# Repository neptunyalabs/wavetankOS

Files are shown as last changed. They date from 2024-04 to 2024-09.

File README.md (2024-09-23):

# What Is This:
Wavetank OS is a do-it-yourself wave tank solution. For those in need of an in-office or in-classroom wavetank with a cloud based (AWS S3) data acquisition program this might be the cheapest & easiest way to get started. 

> [!CAUTION]
> This project comes with no guarantee of performance, or safety. In fact with the combination of electricity and a few hundred gallons of water, as well as fast moving mechanical parts We suggest only experienced makers attempt this project as there are many ways to hurt or kill yourself.

#### The Wavetank
The completed wave tank shown below
Wave Tank Example

#### Example Data
Example data quality post-processed with the `wavepost` utility
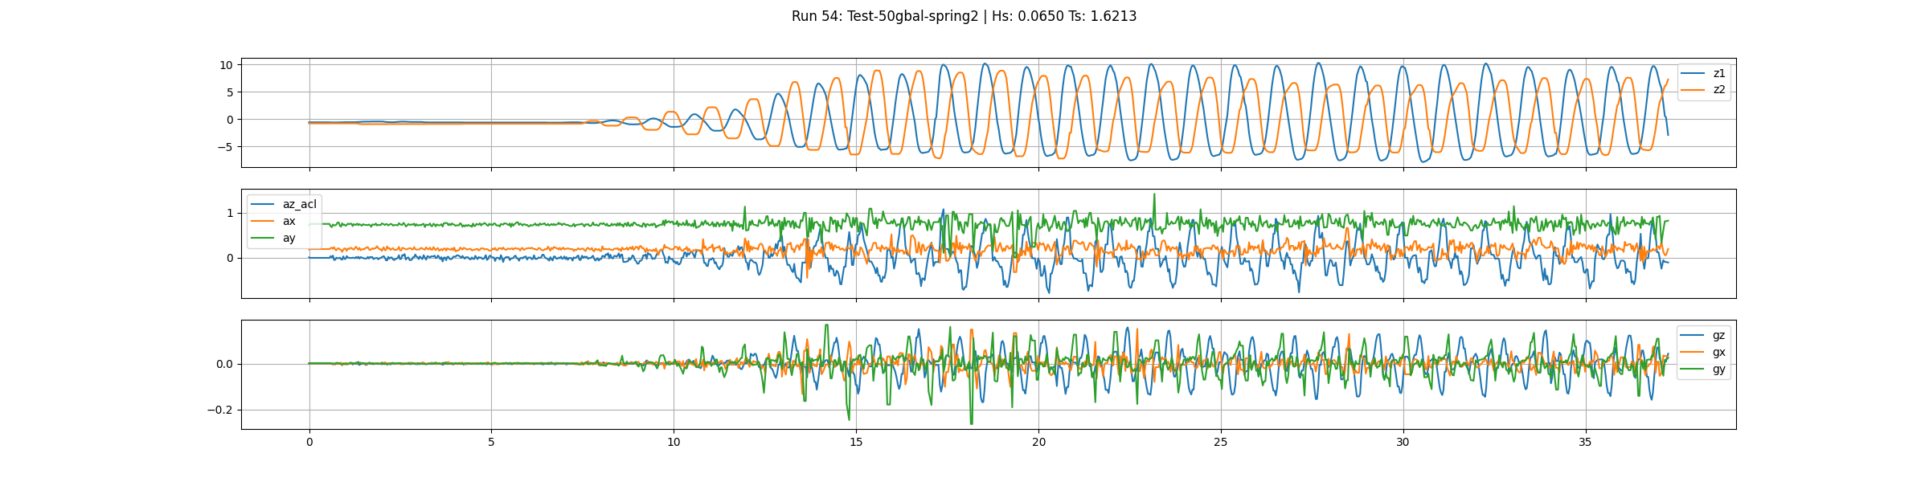
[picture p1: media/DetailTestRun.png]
Example Run


# What Is Included:
1. a set of structural plans, a bom, and construction guidance for the physical wavetank.
2. a bill of materials for electronic components as well as pcb schematics and design files. The design only requires soldering connections and headers so this is beginner friendly
3. this python package that runs a S3 data acquisition, wave maker control, and a live dashboard service to control and view the data in real time, based on pigpio.
4. electronics & software setup guide
5. a post-processing data cli `wavepost` that pulls data from S3 storage and creates graphs of each test run

#  What kind of measurements are provided:
- 4 Encoder positions with RS-485 differential output, we recommend using a magnetic linear scale for its no friction, waterproof design.
- 4 Ultrasonic Distance channels available for capturing wave height.
- Several Channels Of ADC with a dedicated IC chip.
- An integration with an MPU9250 9 axis (Accel,Gyro,Magnetometer) capture
- A few extra outputs for I2C and debugging
- Proven data-rate is between 100 samples per second to S3 storage.

# How To:
Below you'll find a mostly complete set of items you'll need to have to construct the wavetank system.

### Construction Instructions:
1. Tank Construction & Assembly [here](CONSTRUCTION.md)
2. Electronics Construction Overview [here](ELECTRONICS.md)

### Bill of Materials (BOM)
The bill of materials is located here, if you have questions on something feel free to leave a comment, or if you want to contribute an alternative idea feel free suggest alternatives.
https://docs.google.com/spreadsheets/d/107yxzDKXDjfQvaocU3NCo5I_NLpH0Xee_oWynt8TL3E/edit?usp=sharing

### PCB Design Files:
You can order your PCB's from this website, as well as modify the design. If you do make significant improvements to the design please fork this project and submit a PR with your design files.
https://oshwlab.com/neptunya/waveware

### Project Share Folder:
Please see additional media for the construction of the wave tank or assembly of the electronics
https://drive.google.com/drive/folders/0AGw2YOvWZK7JUk9PVA

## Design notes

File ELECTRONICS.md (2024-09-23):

# Electronics Assembly

## Hardware Setup

### PCB Overview
the PCB acts as a connection between the raspberry pi and a number of peripheral sensors and actuators.
#TODO: connections & placement overview (photo)
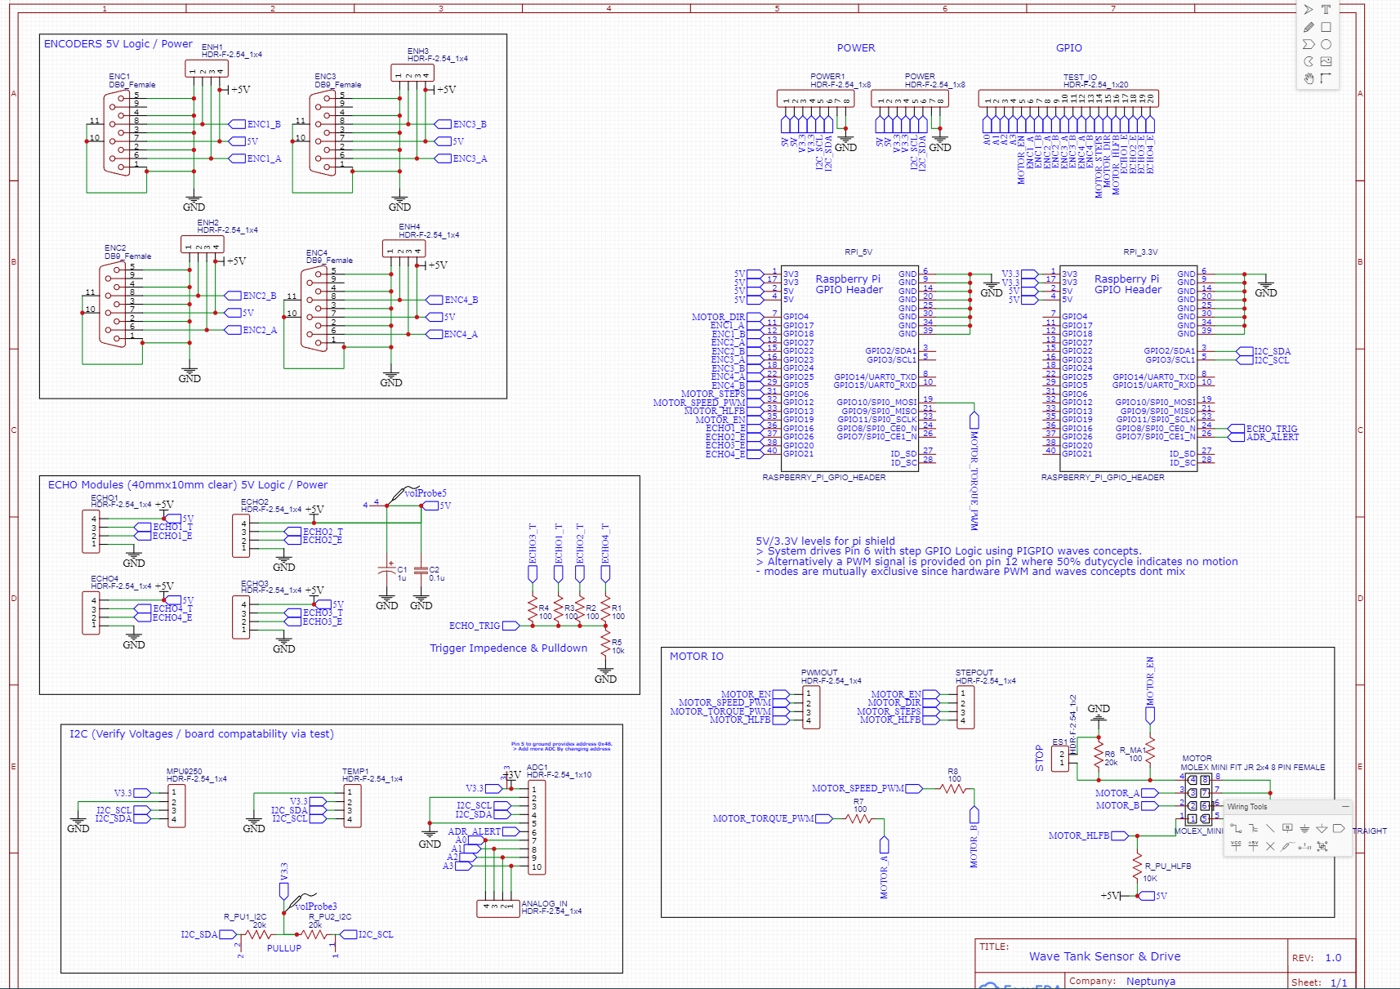
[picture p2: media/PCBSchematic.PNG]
PCB Schematic


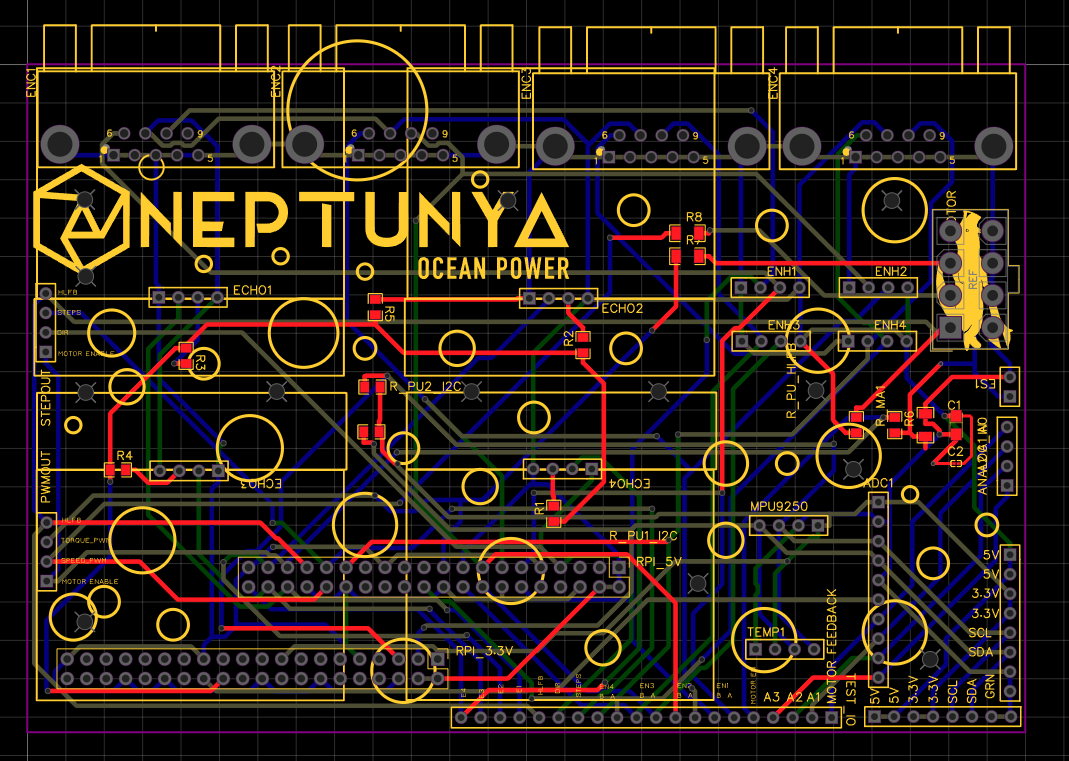
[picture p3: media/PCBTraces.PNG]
PCB Board


## Linux Setup
1. Using the BOM below find the purchase & setup links for the raspberry pi and install ubuntu 20.04 or later
2. Once installed & booted, either log on remotely using SSH or using a mouse & keyboard then navigate to the home directory using `cd ~/`
3. Download the setup script to install all utilities 
```
curl https://raw.githubusercontent.com/neptunyalabs/wavetankOS/main/setup.sh -o wavetankOS_install.sh
```

4. Install wavetankOS, this will enable the wavetank service to start on startup. 
```
bash ~/wavetankOS_install.sh
```
5. If you'd like to use AWS S3 data logging you will need to configure your aws account by adding the account apikey and secret in the environmental variable section, or use another method that AWS provides with their BOTO3 CLI utility. Try running `aws configure` to get started.

Your wavetank dashboard will now be running here `http://<your_hostname>.local:8050/`

### Setting Up The Software:
Configuration of the software is handled through environmental variables, these can be edited for the wavetank service by editing the `/lib/systemd/system/wavetank.service` file on your raspberry pi

This example `service` created in a bash "one-liner" lists the environmental variable defaults
```
sudo bash -c '/bin/cat <<EOM >"/lib/systemd/system/wavetank.service"
[Unit]
WaveTankOS Firmware & Dashboard
[Service]
ExecStart=/home/$(whoami)/wavetankOS/waveware/fw_main.py
ExecStop=/bin/systemctl kill -s SIGKILL wavetank
Type=forking

#here are the potential enviornmental varables for your use
#Environment="WAVEWARE_LOG_S3=true"
#Environment="WAVEWARE_S3_BUCKET=custom_aws_bucket_name" 
#Environment="WAVEWARE_FLDR_NAME=v1" 
#Environment="WAVEWARE_PORT=8777"  #where to run the daq / control api
#Environment="FW_HOST=0.0.0.0"  #where to run the daq / control api
#Environment="WAVEWARE_VWAVE_DIRECT=true"  #control based on speed with correction
#Environment="WAVE_SPEED_DRIVE_MODE=pwm"  #use 'step','pwm','off','step-pwm' depending on your motor type

#Dashboard Customization
#Environment="WAVEWARE_DASH_GRAPH_UPT=3.3"
#Environment="WAVEWARE_DASH_READ_UPT=1.5"

#DAQ Rates
#Environment="WAVEWARE_POLL_RATE=0.033"
#Environment="WAVEWARE_POLL_TEMP=60"
#Environment="WAVEWARE_WINDOW=6" #wavelengths to show for buffer size

[Install]
WantedBy=multi-user.target

EOM'
```

Additionally you can change any one of these when running manually using instructions below.

##### Running Manually:
1. stop the wavetank service `sudo systemctl stop wavetank`
2. use `wavedash` to run the live dashboard
3. use `wavedaq` to run the data acquisition system and control system
4. use `wavepost` to run a post-processing system that downloads data from S3, use `wavepost -h` to determine options. Set the test-data download directory to `WAVEWARE_TESTDATA_FLDR` as the root, then to the `WAVEWARE_FLDR_NAME` of your test data, by default this will be `V1` and must match the data on S3 to be successful. 

### Using The Software:
While using a computer on the same network as the raspberry pi navigate to `http://<your_hostname>.local:8050/` in your browser of choice.

#### Dashboard Overview
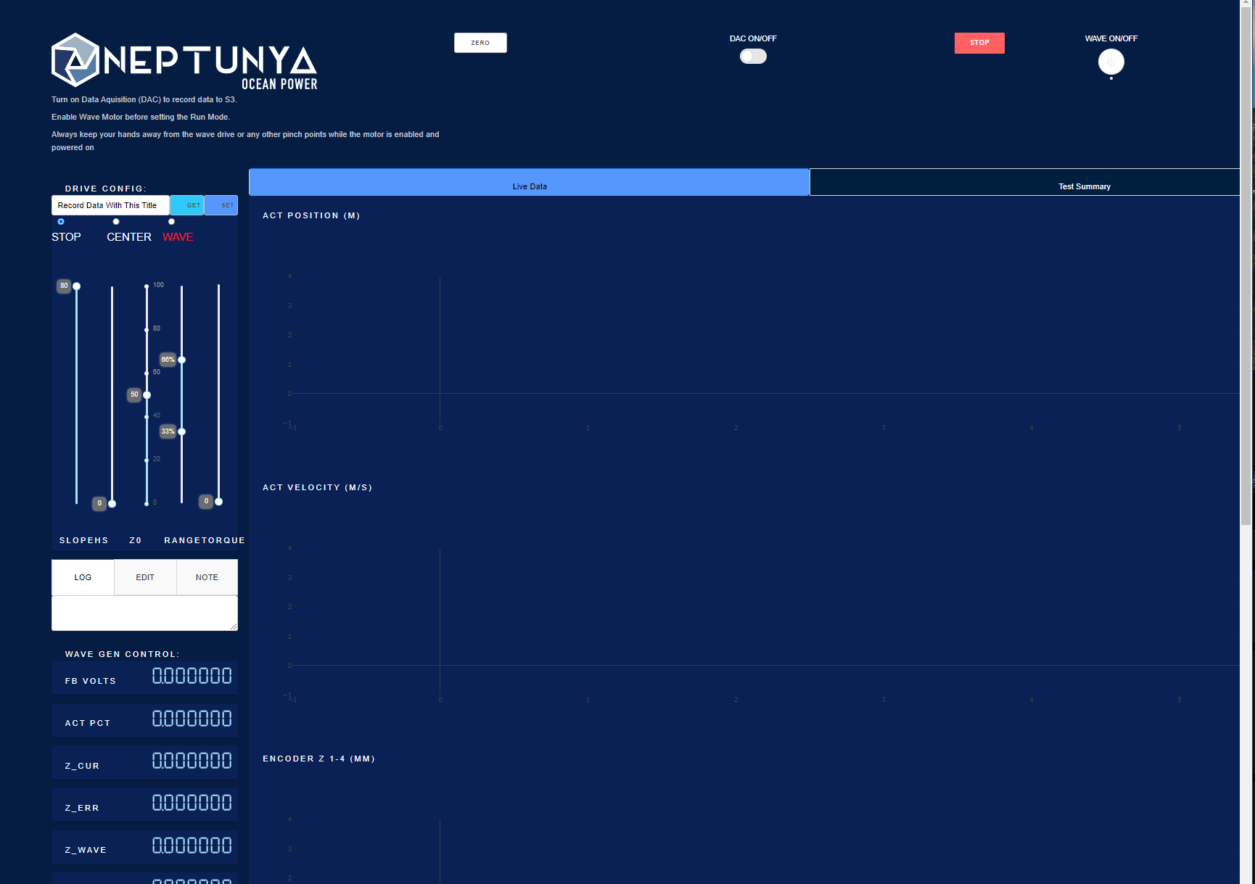
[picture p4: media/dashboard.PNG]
Dashboard Overview


##### Drive Config Section:
1. enable the motor controller with the `wave on/off` button
2. mode input sets the drive mode for the wave maker. Use the get/set buttons to apply changes or get the current state of the wavemaker drive.
3. Set the mode of operation, it is recommened to center first towards the `Zo` input that is a value of 1-100 between the `range` slider values.
4. set the wave height and slope `(wave length x0.5/ wave height)`
5. Using the clearpath PWM mode allows setting torque at right
6. At any time press the red stop button and the drive config will be set to stop. It is safter to use a power cutoff to the motor driver but this works as well.

##### Data Output:
1. encoder readouts can be zero'd by using the zero button. This is useful for ensuring zero is at some datum.
2. By turning on the DAQ with the slider data will start populating from the running daq application.
3. the readouts and positions on the graphs will update as your tests goes on and as long as the daq is on.
4. Finally the test-summary allows a review of all test-points run and their stats.

##### Logging / Customization & Test Notes:
1. The test-note function allows the recording to S3 of test-notes to help with recording intent of tests, or anomolies in the process, or record any other data that you want.
2. The edit tab allows safe setting & adjustment of control system parameters and other internal variables. This can be dangerous however restarting the process or device will fix any error.
3. Finally the log will display the feedback of the DAQ & Control system to give the user an idea of what is going on.

##### Post Processing:
you can easily download your processed data as either a csv or image by using this command. Be sure to set `WAVEWARE_FLDR_NAME` for the output of your data, or use both `WAVEWARE_TESTDATA_DIR` \ `WAVEWARE_FLDR_NAME` as your root folder. This defaults to the fifth folder above the postprocessing file, you've been warned!
```bash
wavepost --run-all --run-all
```

An example set of data is shown below
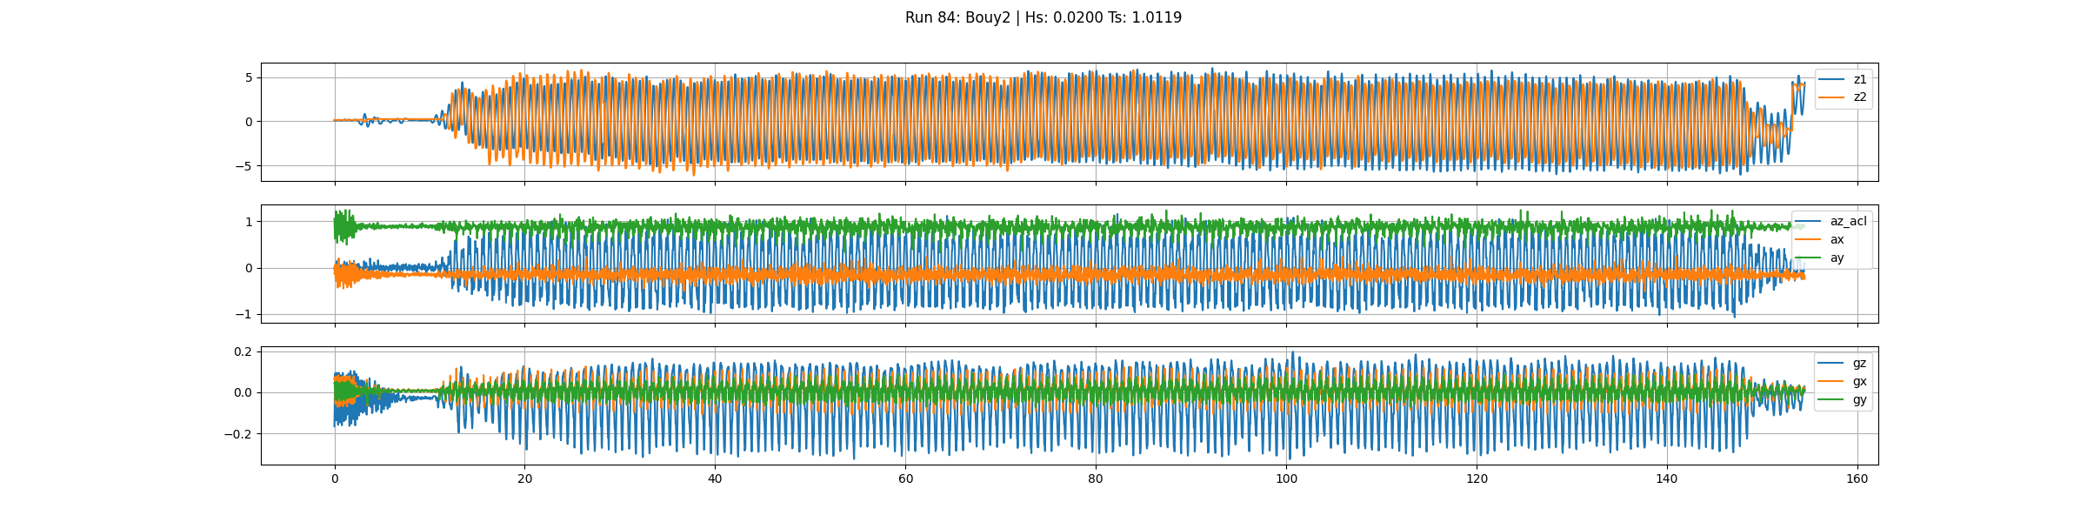
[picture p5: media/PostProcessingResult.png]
Example Run


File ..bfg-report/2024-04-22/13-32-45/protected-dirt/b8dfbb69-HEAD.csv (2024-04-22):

ced399110c0df26b337886e9e83973beb425e1ad | MODIFY | regular-file | waveware/data_aquisition.py | 17888 | 30-31
aa43c4ad8a265b8b6bcb965b1496623cb526297e | MODIFY | regular-file | waveware/load_s3_data.py | 9917 | 41-42

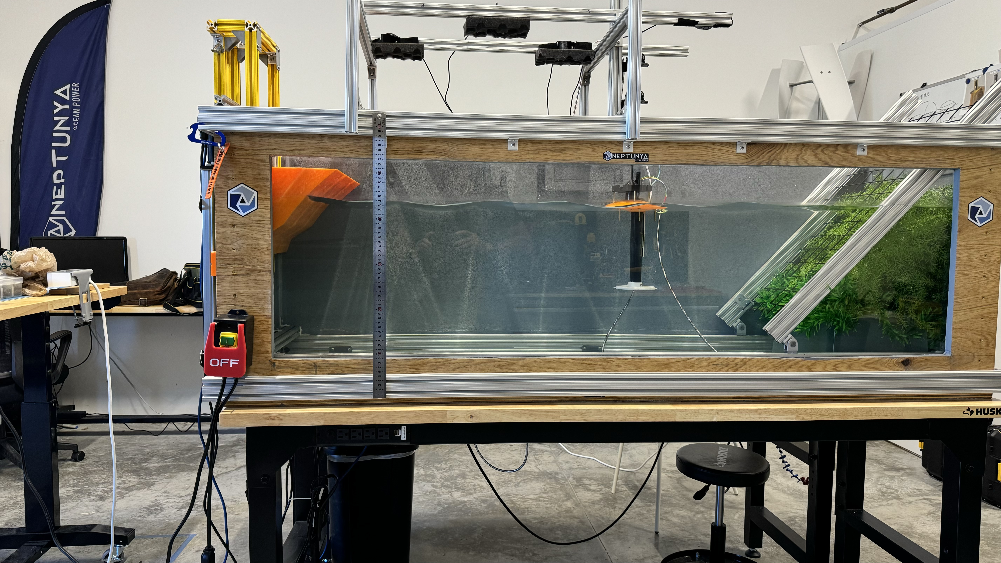
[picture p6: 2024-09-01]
media/wave_tank_overview.jpeg

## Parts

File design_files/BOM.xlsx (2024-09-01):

ITEM | NOTES | DIMENSIONS | UNIT | QTY | UNIT COST | TOTAL COST | LINK | STATUS
STRUCTURE
Non-tempered Glass | safety factor of 2.5 | 1/2'' x 69'' (L) x 21.5'' (W) | Inch | 1 |  |  |  | pending
Plywood sheets (Hardwood) | pre-sanded, non-treated, furniture grade | 3/4'' x 8' (L) x 4' (W) | Feet | 2 | $80.28 | $160.56 | https://www.homedepot.com/p/PureBond-3-4-in-x-4-ft-x-8-ft-Poplar-Hardwood-Plywood-5787/317372919 | purchased
Hardwood Square Dowel | 132'' needed (10' x 6; 36'' x 2) | 3/4'' (W) x 3/4'' (H) x 36'' (L) | Inch | 4 | $3.96 | $15.84 | https://www.homedepot.com/p/Waddell-8312U-3-4-in-x-3-4-in-x-36-in-Hardwood-Square-Dowel-10001817/203334084 | purchased
~~Furring Strip Board~~ | ~~515 1/2" needed (72" x4; 14 3/4" x 10; 20" x 4)~~ | ~~1'' x 96'' (8ft.) (L) x 3'' (W)~~ | ~~Inch~~ | ~~6~~ | ~~$2.48~~ | ~~$14.88~~ | ~~https://www.homedepot.com/p/1-in-x-3-in-x-8-ft-Furring-Strip-Board-164704/100094214~~ | ~~NOT NEEDED~~
ADHESION
Deck Screw | Coarse Thread Sharp Point Polymer Coated | #8 x 2'' | Inch | 2 | $9.97 | $19.94 | https://www.homedepot.com/p/Grip-Rite-8-x-2-in-Phillips-Bugle-Head-Coarse-Thread-Sharp-Point-Polymer-Coated-Exterior-Screws-1-lb-Pack-PTN2S1/100197689 | purchased
Wood Gule | Polyurethane Construction Adhesive | 28 oz. | Ounce | 1 | $12.48 | $12.48 | https://www.homedepot.com/p/Loctite-PL-Premium-28-oz-Polyurethane-Construction-Adhesive-Tan-Cartridge-each-1390594/202020474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 | purchased
Silicone Cement | All-season Aquarium-safe Waterproof | 2.7 oz. | Ounce | 10 | $6.28 | $62.80 | https://www.homedepot.com/p/Loctite-Silicone-Waterproof-Multipurpose-Adhesive-Sealant-2-7-oz-Clear-Tube-each-908570/303769575 | purchased
Fiberglass Cloth Tape |  | 4'' (W) x 99' (L) | Tap | 1 | $11.99 | $11.99 | https://www.amazon.com/Fiberglass-Adhesive-Reinforced-Winding-Molding/dp/B0CBWTM6Q1?s=industrial | purchased
Total Protect Epoxy Barrier Coat Primer | 28 sq ft. needed | 1 gal. (225 sq ft) | Gallon | 1 | $124.99 | $124.99 | https://www.totalboat.com/products/totalprotect-epoxy-barrier-coat-primer?variant=43148111773920 | purchased
Epoxy Primer Thinner 200 |  | 1 qt. (0.25 gal,) | Quart | 1 | $26.99 | $26.99 | https://www.totalboat.com/products/epoxy-primer-thinner-200-solvent | purchased
Wet Edge Topside Paint | Navy Bule | 1 gal. (225 sq ft) | Gallon | 1 | $124.99 | $124.99 | https://www.totalboat.com/products/wet-edge-marine-topside-paint | not needed
~~Epoxy Coating (Clear)~~ | ~~28 sq ft. needed Chemical resistance Low VOC Non-toxic Good resistance to abrasion~~ | ~~1 gal. (25 sq ft)~~ | ~~Gallon~~ | ~~2~~ | ~~$65.96~~ | ~~$131.92~~ | ~~https://www.homedepot.com/p/SIMIRON-TableTop-1-Gal-Clear-High-Gloss-Protective-Epoxy-Coating-40005641/314111463~~
~~Paint ???~~ | ~~Pending???~~ |  |  |  |  | ~~$0.00~~
~~Black Non Toxic Epoxy~~ | ~~28 sq ft. needed~~ | ~~1.5 gal. (37.5 sq ft)~~ | ~~Gallon~~ | ~~1~~ | ~~$187.24~~ | ~~$187.24~~ | ~~https://www.homedepot.com/p/Pond-Armor-Pond-Shield-1-5-gal-Black-Non-Toxic-Epoxy-SKU-BLACK-GA/203886529~~
~~Acetone Thins~~ |  | ~~1 qt. (0.25 gal,)~~ | ~~Quart~~ | ~~1~~ | ~~$10.98~~ | ~~$10.98~~ | ~~https://www.homedepot.com/p/Klean-Strip-1-qt-Acetone-Thins-Fiberglass-Resins-Epoxy-and-Adhesives-QAC18/100144922~~
ELECTRONIC
Reciprocating Linear Actuator Kit Motor | High Torque 40 lbs | 24V150mm120rpm | Set | 1 | $117.99 | $117.99 | https://www.amazon.com/JQDML-Reciprocating-Regulator-Connector-12V150mm95rpm/dp/B095HCVNZC
Gyroscope Acceleration Magnetic Sensor |  |  |  | 1 | $14.99 | $14.99 | https://www.amazon.com/HiLetgo-Gyroscope-Acceleration-Accelerator-Magnetometer/dp/B01I1J0Z7Y?s=industrial
Injection Molding Electronic Ruler Pull Rod Displacement Sensor |  |  |  | 1 | $35.49 | $35.49 | https://www.amazon.com/Injection-Electronic-Displacement-Protection-Stainless/dp/B08BZNV7Q3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
Encoder Magnetic Induction Angle Measurement Sensor |  | 23mm x 23mm (0.91‘’x0.91‘’) | 3pcs | 1 | $9.99 | $9.99 | https://www.amazon.com/Magnetic-Encoder-Induction-Measurement-Precision/dp/B094F8H591?th=1
Tension and Compression Load Cell |  |  |  |  | $137.98 | $0.00 | https://www.ato.com/tension-and-compression-load-cell-1kg-to-200kg?affiliate=shopping&gad_source=1
HARDWARE & SUPLIES
Medium and Large Trigger Clamp | 2 set more |  | Pack | 1 | $36.97 | $36.97 | https://www.homedepot.com/p/DEWALT-Medium-and-Large-Trigger-Clamp-4-Pack-DWHT83196/205086878 | purchased
90-Degree Right Angle Corner Assembly Clamp Squares |  | 4" & 8" (8pcs) | Kit | 1 | $34.99 | $34.99 | https://www.homedepot.com/p/Milescraft-8-in-and-4-in-Squares-Corner-Square-Kit-90-Degree-Right-Angle-Corner-Assembly-Clamp-Squares-8-Piece-7366/319854770 | purchased
Laser Etched Aluminum Rafter Square |  |  |  | 1 | $13.97 | $13.97 | https://www.homedepot.com/p/Empire-7-in-Laser-Etched-Aluminum-Rafter-Square-e2994/205317688 | not needed
Spring Clamp Set |  | 22 pcs | Set | 1 | $9.97 | $9.97 | https://www.homedepot.com/p/Anvil-Spring-Clamp-Set-22-Piece-TGS0199A/302755768 | not needed
 |  |  |  |  |  | $1179.96 | ($5900/kW)

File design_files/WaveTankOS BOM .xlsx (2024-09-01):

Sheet: Overview
WAVETANK OS Bill Of Materials And Purchase Links
LINK TO GITHUB:
https://github.com/neptunyalabs/wavetankOS
LINK TO PCB SCHEMATICS & SPEC
https://oshwlab.com/neptunya/waveware
LINK TO WaveTankOS Share Folder With Media Ect
https://drive.google.com/drive/folders/0AGw2YOvWZK7JUk9PVA
Electronics Cost
1052.97
WARNING: RISK OF INJURY Construction of Wavetank OS involves working with dangerous tools and has the potential to cause injury. Be sure to get assistance if you are not confident that you can complete the steps to assemble this system. Successful construction of the wave tank & wavemaker creates a fast moving, high power actuator that creates a potential point of injury. Further this project involves working with line voltages near water sources. Only attempt this project if you are conident in your ability to handle the risks above
DISCLAIMER: WaveTankOS comes with no garuntee of performance or saftey. use at your own risk

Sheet: Electronics
Major System Components | Number | Cost | Link | Notes | subtotal
 |  | 1052.97 |  |  | 0
Primary Connections |  |  |  |  | 0
PCB Connector Board | 1 | 100 | https://oshwlab.com/neptunya/waveware | See `PCB BOM` For Additional Component Options | 100
Raspberry Pi 4 | 1 | 61.59 | https://www.amazon.com/Raspberry-Model-2019-Quad-Bluetooth/dp/B07TC2BK1X | Be sure to have a microsd card and image with ubuntu and follow these instructions https://ubuntu.com/tutorials/how-to-install-ubuntu-desktop-on-raspberry-pi-4#1-overview | 61.59
120V AC to 5V DC Converter | 1 | 9.98 | https://www.amazon.com/YXQ-100-120V-200-220V-Switch-Converter/dp/B01EYMG3YG | Power Raspberry PCB & Sensors | 9.98
2x20 Ribbon Cables | 1 | 11.74 | https://www.amazon.com/gp/product/B01H53OK5U |  | 11.74
RPI 3.3V Level Shifter | 1 | $28.00 | https://www.amazon.com/Bidirectional-Voltage-Level-Shifter-Raspberry-Converter/dp/B0979BSYCW | Ensure 5V power is connected to 3.3V Side Top Level Power. | $28.00
GFCI Power Supply | 1 | $27.89 | https://www.amazon.com/DEWENWILS-Outdoor-Automatic-Extension-Splitter/dp/B08G4HNCR1 | Prevent Electric Shocks | $27.89
 |  |  |  |  | 0
Sensors |  |  |  |  | 0
MPU9250 | 1 | 14.99 | https://www.amazon.com/HiLetgo-Gyroscope-Acceleration-Accelerator-Magnetometer/dp/B01I1J0Z7Y | Capture Acceleration / Gyro & Magnetic Direction Data | 14.99
I2C Extender (LTC4311) | 1 | 9.99 | https://www.amazon.com/gp/product/B09K6VZPLX | Allows very long I2C lines past 1m in length | 9.99
Temp Sensor (Si7021) | 1 | 15.92 | https://www.amazon.com/SparkFun-Humidity-Temperature-Sensor-Breakout/dp/B01FIJ3MP2/ | Record Temperature & Humdiity | 15.92
4CH ADC Sensor (ADS1115) | 1 | 15.99 | https://www.amazon.com/gp/product/B07VPFLSMX | High Accuracy Analog Voltage Measurements CH0 is for actuator feedback | 15.99
Echo Sensors | 2 | $17.49 | https://www.amazon.com/HiLetgo-Integrated-Ultrasonic-Transducer-Waterproof/dp/B07X5H77T7 |  | $34.98
Magnetic Linear Scale (Differential Encoder) | 2 | $30.62 | https://www.aliexpress.us/item/3256802783796885.html | High Precision Waterproof Contactless Displacement Sensor | $61.24
Restive Linear Displacement (for actuator) 0.3m | 1 | $60.31 | https://www.amazon.com/Injection-Electronic-Displacement-Protection-Stainless/dp/B08BZNV7Q3 | IP67 Waterproof / Actuator Feedback | $60.31
 |  |  |  |  | 0
Misc |  |  |  |  | 0
Connection Wire | 1 | $14.98 | https://www.amazon.com/TUOFENG-Electronic-Prototyping-Circuits-Breadboarding/dp/B07TX6BX47 |  | $14.98
2.54mm headers | 1 | $17.99 | https://www.amazon.com/Glarks-Straight-Connector-Assortment-Prototype/dp/B09BDX9L66 | Use to plugin sensor boards | $17.99
2.54mm screw terminals | 1 | $15.49 | https://www.amazon.com/Molence-Terminal-Connector-Terminals-26-18AWG/dp/B09F6TC7RP | More reliable way to connect wires | $15.49
 |  |  |  |  | 0
Housing |  |  |  |  | 0
Waterproof Housing | 0-1 |  | https://a.co/d/dBAQZih | Keep Stuff Dry | #VALUE!
Waterproof Bulkhead Fitting | 0 |  | https://www.amazon.com/Waterproof-Adjustable-Connectors-Plastic-Protectors/dp/B085NVDC3K | No Leaks! | 0
 |  |  |  |  | 0
Motor (Clearpath Shown) |  |  |  |  | 0
Linear Ball-Screw Actuator | 1 | $100 |  | - stroke: 400mm (19") - lead: 5mm (single-start) | $100
Clearpath Motor DC Power Supply | 1 | $200 | https://teknic.com/products/servo-motor-dc-power-supply/ | - 75 VDC / 3 A output - 225 Watts continuous power | $200
Clearpath Motor | 1 | $300 | https://teknic.com/model-info/CPM-MCVC-2331P-RLN/ | CPM-MCVC-2331P-RLN servo-motor - speed: 4000 rpm - torque: 0.40 Nm - power: 184 W (0.25 hp) | $300
Emergency Stop | 1 |  | https://www.amazon.com/Dreyoo-Single-Contact-Electrical-Equipment/dp/B0C9QD72SL | Attach Motor Controller To this | 0
 |  |  |  |  | 0
 |  |  |  |  | 0
 |  |  |  |  | 0
 |  |  |  |  | 0
 |  |  |  |  | 0
 |  |  |  |  | 0
 |  |  |  |  | 0
 |  |  |  |  | 0
 |  |  |  |  | 0
 |  |  |  |  | 0
 |  |  |  |  | 0
 |  |  |  |  | 0
 |  |  |  |  | 0
 |  |  |  |  | 0
 |  |  |  |  | 0
 |  |  |  |  | 0
 |  |  |  |  | 0
 |  |  |  |  | 0
 |  |  |  |  | 0
 |  |  |  |  | 0
 |  |  |  |  | 0
 |  |  |  |  | 0
 |  |  |  |  | 0
 |  |  |  |  | 0
 |  |  |  |  | 0
 |  |  |  |  | 0
 |  |  |  |  | 0
 |  |  |  |  | 0
 |  |  |  |  | 0
 |  |  |  |  | 0
 |  |  |  |  | 0
 |  |  |  |  | 0
 |  |  |  |  | 0
 |  |  |  |  | 0
 |  |  |  |  | 0
 |  |  |  |  | 0
 |  |  |  |  | 0
 |  |  |  |  | 0
 |  |  |  |  | 0
 |  |  |  |  | 0
 |  |  |  |  | 0
 |  |  |  |  | 0
 |  |  |  |  | 0
 |  |  |  |  | 0
 |  |  |  |  | 0
 |  |  |  |  | 0
 |  |  |  |  | 0
 |  |  |  |  | 0
 |  |  |  |  | 0
 |  |  |  |  | 0
 |  |  |  |  | 0
 |  |  |  |  | 0
 |  |  |  |  | 0
 |  |  |  |  | 0
 |  |  |  |  | 0
 |  |  |  |  | 0
 |  |  |  |  | 0
 |  |  |  |  | 0
 |  |  |  |  | 0
 |  |  |  |  | 0
 |  |  |  |  | 0
 |  |  |  |  | 0
 |  |  |  |  | 0
 |  |  |  |  | 0
 |  |  |  |  | 0
 |  |  |  |  | 0
 |  |  |  |  | 0
 |  |  |  |  | 0
 |  |  |  |  | 0
 |  |  |  |  | 0
 |  |  |  |  | 0
 |  |  |  |  | 0
 |  |  |  |  | 0
 |  |  |  |  | 0
 |  |  |  |  | 0
 |  |  |  |  | 0
 |  |  |  |  | 0
 |  |  |  |  | 0
 |  |  |  |  | 0
 |  |  |  |  | 0
 |  |  |  |  | 0
 |  |  |  |  | 0
 |  |  |  |  | 0
 |  |  |  |  | 0
 |  |  |  |  | 0
 |  |  |  |  | 0
 |  |  |  |  | 0
 |  |  |  |  | 0
 |  |  |  |  | 0
 |  |  |  |  | 0
 |  |  |  |  | 0
 |  |  |  |  | 0
 |  |  |  |  | 0
 |  |  |  |  | 0
 |  |  |  |  | 0
 |  |  |  |  | 0
 |  |  |  |  | 0
 |  |  |  |  | 0
 |  |  |  |  | 0
 |  |  |  |  | 0
 |  |  |  |  | 0
 |  |  |  |  | 0
 |  |  |  |  | 0
 |  |  |  |  | 0
 |  |  |  |  | 0
 |  |  |  |  | 0
 |  |  |  |  | 0
 |  |  |  |  | 0
 |  |  |  |  | 0
 |  |  |  |  | 0
 |  |  |  |  | 0
 |  |  |  |  | 0
 |  |  |  |  | 0
 |  |  |  |  | 0
 |  |  |  |  | 0
 |  |  |  |  | 0
 |  |  |  |  | 0
 |  |  |  |  | 0
 |  |  |  |  | 0
 |  |  |  |  | 0
 |  |  |  |  | 0
 |  |  |  |  | 0
 |  |  |  |  | 0
 |  |  |  |  | 0
 |  |  |  |  | 0
 |  |  |  |  | 0
 |  |  |  |  | 0
 |  |  |  |  | 0
 |  |  |  |  | 0
 |  |  |  |  | 0
 |  |  |  |  | 0
 |  |  |  |  | 0
 |  |  |  |  | 0
 |  |  |  |  | 0
 |  |  |  |  | 0
 |  |  |  |  | 0
 |  |  |  |  | 0
 |  |  |  |  | 0
 |  |  |  |  | 0
 |  |  |  |  | 0
 |  |  |  |  | 0
 |  |  |  |  | 0
 |  |  |  |  | 0
 |  |  |  |  | 0
 |  |  |  |  | 0
 |  |  |  |  | 0
 |  |  |  |  | 0
 |  |  |  |  | 0
 |  |  |  |  | 0
 |  |  |  |  | 0
 |  |  |  |  | 0
 |  |  |  |  | 0
 |  |  |  |  | 0
 |  |  |  |  | 0
 |  |  |  |  | 0
 |  |  |  |  | 0
 |  |  |  |  | 0
 |  |  |  |  | 0
 |  |  |  |  | 0
 |  |  |  |  | 0
 |  |  |  |  | 0
 |  |  |  |  | 0
 |  |  |  |  | 0
 |  |  |  |  | 0
 |  |  |  |  | 0
 |  |  |  |  | 0
 |  |  |  |  | 0
 |  |  |  |  | 0
 |  |  |  |  | 0
 |  |  |  |  | 0
 |  |  |  |  | 0
 |  |  |  |  | 0
 |  |  |  |  | 0
 |  |  |  |  | 0
 |  |  |  |  | 0
 |  |  |  |  | 0
 |  |  |  |  | 0
 |  |  |  |  | 0
 |  |  |  |  | 0
 |  |  |  |  | 0
 |  |  |  |  | 0
 |  |  |  |  | 0
 |  |  |  |  | 0
 |  |  |  |  | 0
 |  |  |  |  | 0
 |  |  |  |  | 0
 |  |  |  |  | 0
 |  |  |  |  | 0
 |  |  |  |  | 0
 |  |  |  |  | 0
 |  |  |  |  | 0
 |  |  |  |  | 0
 |  |  |  |  | 0
 |  |  |  |  | 0
 |  |  |  |  | 0
 |  |  |  |  | 0
 |  |  |  |  | 0
 |  |  |  |  | 0
 |  |  |  |  | 0
 |  |  |  |  | 0
 |  |  |  |  | 0
 |  |  |  |  | 0
 |  |  |  |  | 0
 |  |  |  |  | 0
 |  |  |  |  | 0
 |  |  |  |  | 0
 |  |  |  |  | 0
 |  |  |  |  | 0
 |  |  |  |  | 0
 |  |  |  |  | 0
 |  |  |  |  | 0
 |  |  |  |  | 0
 |  |  |  |  | 0
 |  |  |  |  | 0
 |  |  |  |  | 0
 |  |  |  |  | 0
 |  |  |  |  | 0
 |  |  |  |  | 0
 |  |  |  |  | 0
 |  |  |  |  | 0
 |  |  |  |  | 0
 |  |  |  |  | 0
 |  |  |  |  | 0
 |  |  |  |  | 0
 |  |  |  |  | 0
 |  |  |  |  | 0
 |  |  |  |  | 0
 |  |  |  |  | 0
 |  |  |  |  | 0
 |  |  |  |  | 0
 |  |  |  |  | 0
 |  |  |  |  | 0
 |  |  |  |  | 0
 |  |  |  |  | 0
 |  |  |  |  | 0
 |  |  |  |  | 0
 |  |  |  |  | 0
 |  |  |  |  | 0
 |  |  |  |  | 0
 |  |  |  |  | 0
 |  |  |  |  | 0
 |  |  |  |  | 0
 |  |  |  |  | 0
 |  |  |  |  | 0
 |  |  |  |  | 0
 |  |  |  |  | 0
 |  |  |  |  | 0
 |  |  |  |  | 0
 |  |  |  |  | 0
 |  |  |  |  | 0
 |  |  |  |  | 0
 |  |  |  |  | 0
 |  |  |  |  | 0
 |  |  |  |  | 0
 |  |  |  |  | 0
 |  |  |  |  | 0
 |  |  |  |  | 0
 |  |  |  |  | 0
 |  |  |  |  | 0
 |  |  |  |  | 0
 |  |  |  |  | 0
 |  |  |  |  | 0
 |  |  |  |  | 0
 |  |  |  |  | 0
 |  |  |  |  | 0
 |  |  |  |  | 0
 |  |  |  |  | 0
 |  |  |  |  | 0
 |  |  |  |  | 0
 |  |  |  |  | 0
 |  |  |  |  | 0
 |  |  |  |  | 0
 |  |  |  |  | 0
 |  |  |  |  | 0
 |  |  |  |  | 0
 |  |  |  |  | 0
 |  |  |  |  | 0
 |  |  |  |  | 0
 |  |  |  |  | 0
 |  |  |  |  | 0
 |  |  |  |  | 0
 |  |  |  |  | 0
 |  |  |  |  | 0
 |  |  |  |  | 0
 |  |  |  |  | 0
 |  |  |  |  | 0
 |  |  |  |  | 0
 |  |  |  |  | 0
 |  |  |  |  | 0
 |  |  |  |  | 0
 |  |  |  |  | 0
 |  |  |  |  | 0
 |  |  |  |  | 0
 |  |  |  |  | 0
 |  |  |  |  | 0
 |  |  |  |  | 0
 |  |  |  |  | 0
 |  |  |  |  | 0
 |  |  |  |  | 0
 |  |  |  |  | 0
 |  |  |  |  | 0
 |  |  |  |  | 0
 |  |  |  |  | 0
 |  |  |  |  | 0
 |  |  |  |  | 0
 |  |  |  |  | 0
 |  |  |  |  | 0
 |  |  |  |  | 0
 |  |  |  |  | 0
 |  |  |  |  | 0
 |  |  |  |  | 0
 |  |  |  |  | 0
 |  |  |  |  | 0
 |  |  |  |  | 0
 |  |  |  |  | 0
 |  |  |  |  | 0
 |  |  |  |  | 0
 |  |  |  |  | 0
 |  |  |  |  | 0
 |  |  |  |  | 0
 |  |  |  |  | 0
 |  |  |  |  | 0
 |  |  |  |  | 0
 |  |  |  |  | 0
 |  |  |  |  | 0
 |  |  |  |  | 0
 |  |  |  |  | 0
 |  |  |  |  | 0
 |  |  |  |  | 0
 |  |  |  |  | 0
 |  |  |  |  | 0
 |  |  |  |  | 0
 |  |  |  |  | 0
 |  |  |  |  | 0
 |  |  |  |  | 0
 |  |  |  |  | 0
 |  |  |  |  | 0
 |  |  |  |  | 0
 |  |  |  |  | 0
 |  |  |  |  | 0
 |  |  |  |  | 0
 |  |  |  |  | 0
 |  |  |  |  | 0
 |  |  |  |  | 0
 |  |  |  |  | 0
 |  |  |  |  | 0
 |  |  |  |  | 0
 |  |  |  |  | 0
 |  |  |  |  | 0
 |  |  |  |  | 0
 |  |  |  |  | 0
 |  |  |  |  | 0
 |  |  |  |  | 0
 |  |  |  |  | 0
 |  |  |  |  | 0
 |  |  |  |  | 0
 |  |  |  |  | 0
 |  |  |  |  | 0
 |  |  |  |  | 0
 |  |  |  |  | 0
 |  |  |  |  | 0
 |  |  |  |  | 0
 |  |  |  |  | 0
 |  |  |  |  | 0
 |  |  |  |  | 0
 |  |  |  |  | 0
 |  |  |  |  | 0
 |  |  |  |  | 0
 |  |  |  |  | 0
 |  |  |  |  | 0
 |  |  |  |  | 0
 |  |  |  |  | 0
 |  |  |  |  | 0
 |  |  |  |  | 0
 |  |  |  |  | 0
 |  |  |  |  | 0
 |  |  |  |  | 0
 |  |  |  |  | 0
 |  |  |  |  | 0
 |  |  |  |  | 0
 |  |  |  |  | 0
 |  |  |  |  | 0
 |  |  |  |  | 0
 |  |  |  |  | 0
 |  |  |  |  | 0
 |  |  |  |  | 0
 |  |  |  |  | 0
 |  |  |  |  | 0
 |  |  |  |  | 0
 |  |  |  |  | 0
 |  |  |  |  | 0
 |  |  |  |  | 0
 |  |  |  |  | 0
 |  |  |  |  | 0
 |  |  |  |  | 0
 |  |  |  |  | 0
 |  |  |  |  | 0
 |  |  |  |  | 0
 |  |  |  |  | 0
 |  |  |  |  | 0
 |  |  |  |  | 0
 |  |  |  |  | 0
 |  |  |  |  | 0
 |  |  |  |  | 0
 |  |  |  |  | 0
 |  |  |  |  | 0
 |  |  |  |  | 0
 |  |  |  |  | 0
 |  |  |  |  | 0
 |  |  |  |  | 0
 |  |  |  |  | 0
 |  |  |  |  | 0
 |  |  |  |  | 0
 |  |  |  |  | 0
 |  |  |  |  | 0
 |  |  |  |  | 0
 |  |  |  |  | 0
 |  |  |  |  | 0
 |  |  |  |  | 0
 |  |  |  |  | 0
 |  |  |  |  | 0
 |  |  |  |  | 0
 |  |  |  |  | 0
 |  |  |  |  | 0
 |  |  |  |  | 0
 |  |  |  |  | 0
 |  |  |  |  | 0
 |  |  |  |  | 0
 |  |  |  |  | 0
 |  |  |  |  | 0
 |  |  |  |  | 0
 |  |  |  |  | 0
 |  |  |  |  | 0
 |  |  |  |  | 0
 |  |  |  |  | 0
 |  |  |  |  | 0
 |  |  |  |  | 0
 |  |  |  |  | 0
 |  |  |  |  | 0
 |  |  |  |  | 0
 |  |  |  |  | 0
 |  |  |  |  | 0
 |  |  |  |  | 0
 |  |  |  |  | 0
 |  |  |  |  | 0
 |  |  |  |  | 0
 |  |  |  |  | 0
 |  |  |  |  | 0
 |  |  |  |  | 0
 |  |  |  |  | 0
 |  |  |  |  | 0
 |  |  |  |  | 0
 |  |  |  |  | 0
 |  |  |  |  | 0
 |  |  |  |  | 0
 |  |  |  |  | 0
 |  |  |  |  | 0
 |  |  |  |  | 0
 |  |  |  |  | 0
 |  |  |  |  | 0
 |  |  |  |  | 0
 |  |  |  |  | 0
 |  |  |  |  | 0
 |  |  |  |  | 0
 |  |  |  |  | 0
 |  |  |  |  | 0
 |  |  |  |  | 0
 |  |  |  |  | 0
 |  |  |  |  | 0
 |  |  |  |  | 0
 |  |  |  |  | 0
 |  |  |  |  | 0
 |  |  |  |  | 0
 |  |  |  |  | 0
 |  |  |  |  | 0
 |  |  |  |  | 0
 |  |  |  |  | 0
 |  |  |  |  | 0
 |  |  |  |  | 0
 |  |  |  |  | 0
 |  |  |  |  | 0
 |  |  |  |  | 0
 |  |  |  |  | 0
 |  |  |  |  | 0
 |  |  |  |  | 0
 |  |  |  |  | 0
 |  |  |  |  | 0
 |  |  |  |  | 0
 |  |  |  |  | 0
 |  |  |  |  | 0
 |  |  |  |  | 0
 |  |  |  |  | 0
 |  |  |  |  | 0
 |  |  |  |  | 0
 |  |  |  |  | 0
 |  |  |  |  | 0
 |  |  |  |  | 0
 |  |  |  |  | 0
 |  |  |  |  | 0
 |  |  |  |  | 0
 |  |  |  |  | 0
 |  |  |  |  | 0
 |  |  |  |  | 0
 |  |  |  |  | 0
 |  |  |  |  | 0
 |  |  |  |  | 0
 |  |  |  |  | 0
 |  |  |  |  | 0
 |  |  |  |  | 0
 |  |  |  |  | 0
 |  |  |  |  | 0
 |  |  |  |  | 0
 |  |  |  |  | 0
 |  |  |  |  | 0
 |  |  |  |  | 0
 |  |  |  |  | 0
 |  |  |  |  | 0
 |  |  |  |  | 0
 |  |  |  |  | 0
 |  |  |  |  | 0
 |  |  |  |  | 0
 |  |  |  |  | 0
 |  |  |  |  | 0
 |  |  |  |  | 0
 |  |  |  |  | 0
 |  |  |  |  | 0
 |  |  |  |  | 0
 |  |  |  |  | 0
 |  |  |  |  | 0
 |  |  |  |  | 0
 |  |  |  |  | 0
 |  |  |  |  | 0
 |  |  |  |  | 0
 |  |  |  |  | 0
 |  |  |  |  | 0
 |  |  |  |  | 0
 |  |  |  |  | 0
 |  |  |  |  | 0
 |  |  |  |  | 0
 |  |  |  |  | 0
 |  |  |  |  | 0
 |  |  |  |  | 0
 |  |  |  |  | 0
 |  |  |  |  | 0
 |  |  |  |  | 0
 |  |  |  |  | 0
 |  |  |  |  | 0
 |  |  |  |  | 0
 |  |  |  |  | 0
 |  |  |  |  | 0
 |  |  |  |  | 0
 |  |  |  |  | 0
 |  |  |  |  | 0
 |  |  |  |  | 0
 |  |  |  |  | 0
 |  |  |  |  | 0
 |  |  |  |  | 0
 |  |  |  |  | 0
 |  |  |  |  | 0
 |  |  |  |  | 0
 |  |  |  |  | 0
 |  |  |  |  | 0
 |  |  |  |  | 0
 |  |  |  |  | 0
 |  |  |  |  | 0
 |  |  |  |  | 0
 |  |  |  |  | 0
 |  |  |  |  | 0
 |  |  |  |  | 0
 |  |  |  |  | 0
 |  |  |  |  | 0
 |  |  |  |  | 0
 |  |  |  |  | 0
 |  |  |  |  | 0
 |  |  |  |  | 0
 |  |  |  |  | 0
 |  |  |  |  | 0
 |  |  |  |  | 0
 |  |  |  |  | 0
 |  |  |  |  | 0
 |  |  |  |  | 0
 |  |  |  |  | 0
 |  |  |  |  | 0
 |  |  |  |  | 0
 |  |  |  |  | 0
 |  |  |  |  | 0
 |  |  |  |  | 0
 |  |  |  |  | 0
 |  |  |  |  | 0
 |  |  |  |  | 0
 |  |  |  |  | 0
 |  |  |  |  | 0
 |  |  |  |  | 0
 |  |  |  |  | 0
 |  |  |  |  | 0
 |  |  |  |  | 0
 |  |  |  |  | 0
 |  |  |  |  | 0
 |  |  |  |  | 0
 |  |  |  |  | 0
 |  |  |  |  | 0
 |  |  |  |  | 0
 |  |  |  |  | 0
 |  |  |  |  | 0
 |  |  |  |  | 0
 |  |  |  |  | 0
 |  |  |  |  | 0
 |  |  |  |  | 0
 |  |  |  |  | 0
 |  |  |  |  | 0
 |  |  |  |  | 0
 |  |  |  |  | 0
 |  |  |  |  | 0
 |  |  |  |  | 0
 |  |  |  |  | 0
 |  |  |  |  | 0
 |  |  |  |  | 0
 |  |  |  |  | 0
 |  |  |  |  | 0
 |  |  |  |  | 0
 |  |  |  |  | 0
 |  |  |  |  | 0
 |  |  |  |  | 0
 |  |  |  |  | 0
 |  |  |  |  | 0
 |  |  |  |  | 0
 |  |  |  |  | 0
 |  |  |  |  | 0
 |  |  |  |  | 0
 |  |  |  |  | 0
 |  |  |  |  | 0
 |  |  |  |  | 0
 |  |  |  |  | 0
 |  |  |  |  | 0
 |  |  |  |  | 0
 |  |  |  |  | 0
 |  |  |  |  | 0
 |  |  |  |  | 0
 |  |  |  |  | 0
 |  |  |  |  | 0
 |  |  |  |  | 0
 |  |  |  |  | 0
 |  |  |  |  | 0
 |  |  |  |  | 0
 |  |  |  |  | 0
 |  |  |  |  | 0
 |  |  |  |  | 0
 |  |  |  |  | 0
 |  |  |  |  | 0
 |  |  |  |  | 0
 |  |  |  |  | 0
 |  |  |  |  | 0
 |  |  |  |  | 0
 |  |  |  |  | 0
 |  |  |  |  | 0
 |  |  |  |  | 0
 |  |  |  |  | 0
 |  |  |  |  | 0
 |  |  |  |  | 0
 |  |  |  |  | 0
 |  |  |  |  | 0
 |  |  |  |  | 0
 |  |  |  |  | 0
 |  |  |  |  | 0
 |  |  |  |  | 0
 |  |  |  |  | 0
 |  |  |  |  | 0
 |  |  |  |  | 0
 |  |  |  |  | 0
 |  |  |  |  | 0
 |  |  |  |  | 0
 |  |  |  |  | 0
 |  |  |  |  | 0
 |  |  |  |  | 0
 |  |  |  |  | 0
 |  |  |  |  | 0
 |  |  |  |  | 0
 |  |  |  |  | 0
 |  |  |  |  | 0
 |  |  |  |  | 0
 |  |  |  |  | 0
 |  |  |  |  | 0
 |  |  |  |  | 0
 |  |  |  |  | 0
 |  |  |  |  | 0
 |  |  |  |  | 0
 |  |  |  |  | 0
 |  |  |  |  | 0
 |  |  |  |  | 0
 |  |  |  |  | 0
 |  |  |  |  | 0
 |  |  |  |  | 0
 |  |  |  |  | 0
 |  |  |  |  | 0
 |  |  |  |  | 0
 |  |  |  |  | 0
 |  |  |  |  | 0
 |  |  |  |  | 0
 |  |  |  |  | 0
 |  |  |  |  | 0
 |  |  |  |  | 0
 |  |  |  |  | 0
 |  |  |  |  | 0
 |  |  |  |  | 0
 |  |  |  |  | 0
 |  |  |  |  | 0
 |  |  |  |  | 0
 |  |  |  |  | 0
 |  |  |  |  | 0
 |  |  |  |  | 0
 |  |  |  |  | 0
 |  |  |  |  | 0
 |  |  |  |  | 0
 |  |  |  |  | 0
 |  |  |  |  | 0
 |  |  |  |  | 0
 |  |  |  |  | 0
 |  |  |  |  | 0
 |  |  |  |  | 0
 |  |  |  |  | 0
 |  |  |  |  | 0
 |  |  |  |  | 0
 |  |  |  |  | 0
 |  |  |  |  | 0
 |  |  |  |  | 0
 |  |  |  |  | 0
 |  |  |  |  | 0
 |  |  |  |  | 0
 |  |  |  |  | 0
 |  |  |  |  | 0
 |  |  |  |  | 0
 |  |  |  |  | 0
 |  |  |  |  | 0
 |  |  |  |  | 0
 |  |  |  |  | 0
 |  |  |  |  | 0
 |  |  |  |  | 0
 |  |  |  |  | 0
 |  |  |  |  | 0
 |  |  |  |  | 0
 |  |  |  |  | 0
 |  |  |  |  | 0
 |  |  |  |  | 0
 |  |  |  |  | 0
 |  |  |  |  | 0
 |  |  |  |  | 0
 |  |  |  |  | 0
 |  |  |  |  | 0
 |  |  |  |  | 0
 |  |  |  |  | 0
 |  |  |  |  | 0
 |  |  |  |  | 0
 |  |  |  |  | 0
 |  |  |  |  | 0
 |  |  |  |  | 0
 |  |  |  |  | 0
 |  |  |  |  | 0
 |  |  |  |  | 0
 |  |  |  |  | 0
 |  |  |  |  | 0
 |  |  |  |  | 0
 |  |  |  |  | 0
 |  |  |  |  | 0
 |  |  |  |  | 0
 |  |  |  |  | 0
 |  |  |  |  | 0
 |  |  |  |  | 0
 |  |  |  |  | 0
 |  |  |  |  | 0
 |  |  |  |  | 0
 |  |  |  |  | 0
 |  |  |  |  | 0
 |  |  |  |  | 0
 |  |  |  |  | 0
 |  |  |  |  | 0
 |  |  |  |  | 0
 |  |  |  |  | 0
 |  |  |  |  | 0
 |  |  |  |  | 0
 |  |  |  |  | 0
 |  |  |  |  | 0
 |  |  |  |  | 0
 |  |  |  |  | 0
 |  |  |  |  | 0
 |  |  |  |  | 0
 |  |  |  |  | 0
 |  |  |  |  | 0
 |  |  |  |  | 0
 |  |  |  |  | 0
 |  |  |  |  | 0
 |  |  |  |  | 0
 |  |  |  |  | 0
 |  |  |  |  | 0
 |  |  |  |  | 0
 |  |  |  |  | 0
 |  |  |  |  | 0
 |  |  |  |  | 0
 |  |  |  |  | 0
 |  |  |  |  | 0
 |  |  |  |  | 0
 |  |  |  |  | 0
 |  |  |  |  | 0
 |  |  |  |  | 0
 |  |  |  |  | 0
 |  |  |  |  | 0
 |  |  |  |  | 0
 |  |  |  |  | 0
 |  |  |  |  | 0
 |  |  |  |  | 0
 |  |  |  |  | 0
 |  |  |  |  | 0
 |  |  |  |  | 0
 |  |  |  |  | 0
 |  |  |  |  | 0
 |  |  |  |  | 0
 |  |  |  |  | 0
 |  |  |  |  | 0
 |  |  |  |  | 0
 |  |  |  |  | 0
 |  |  |  |  | 0
 |  |  |  |  | 0
 |  |  |  |  | 0
 |  |  |  |  | 0
 |  |  |  |  | 0
 |  |  |  |  | 0
 |  |  |  |  | 0
 |  |  |  |  | 0
 |  |  |  |  | 0
 |  |  |  |  | 0
 |  |  |  |  | 0
 |  |  |  |  | 0
 |  |  |  |  | 0
 |  |  |  |  | 0
 |  |  |  |  | 0
 |  |  |  |  | 0
 |  |  |  |  | 0
 |  |  |  |  | 0
 |  |  |  |  | 0
 |  |  |  |  | 0
 |  |  |  |  | 0
 |  |  |  |  | 0
 |  |  |  |  | 0
 |  |  |  |  | 0
 |  |  |  |  | 0
 |  |  |  |  | 0
 |  |  |  |  | 0
 |  |  |  |  | 0
 |  |  |  |  | 0
 |  |  |  |  | 0
 |  |  |  |  | 0
 |  |  |  |  | 0
 |  |  |  |  | 0
 |  |  |  |  | 0
 |  |  |  |  | 0
 |  |  |  |  | 0
 |  |  |  |  | 0
 |  |  |  |  | 0
 |  |  |  |  | 0
 |  |  |  |  | 0
 |  |  |  |  | 0
 |  |  |  |  | 0
 |  |  |  |  | 0
 |  |  |  |  | 0
 |  |  |  |  | 0
 |  |  |  |  | 0
 |  |  |  |  | 0
 |  |  |  |  | 0
 |  |  |  |  | 0
 |  |  |  |  | 0
 |  |  |  |  | 0
 |  |  |  |  | 0
 |  |  |  |  | 0
 |  |  |  |  | 0
 |  |  |  |  | 0
 |  |  |  |  | 0
 |  |  |  |  | 0
 |  |  |  |  | 0
 |  |  |  |  | 0
 |  |  |  |  | 0
 |  |  |  |  | 0
 |  |  |  |  | 0
 |  |  |  |  | 0
 |  |  |  |  | 0
 |  |  |  |  | 0
 |  |  |  |  | 0
 |  |  |  |  | 0
 |  |  |  |  | 0
 |  |  |  |  | 0
 |  |  |  |  | 0
 |  |  |  |  | 0
 |  |  |  |  | 0
 |  |  |  |  | 0
 |  |  |  |  | 0
 |  |  |  |  | 0
 |  |  |  |  | 0
 |  |  |  |  | 0
 |  |  |  |  | 0
 |  |  |  |  | 0
 |  |  |  |  | 0
 |  |  |  |  | 0
 |  |  |  |  | 0
 |  |  |  |  | 0
 |  |  |  |  | 0
 |  |  |  |  | 0
 |  |  |  |  | 0
 |  |  |  |  | 0
 |  |  |  |  | 0
 |  |  |  |  | 0
 |  |  |  |  | 0
 |  |  |  |  | 0
 |  |  |  |  | 0
 |  |  |  |  | 0
 |  |  |  |  | 0
 |  |  |  |  | 0
 |  |  |  |  | 0
 |  |  |  |  | 0
 |  |  |  |  | 0
 |  |  |  |  | 0
 |  |  |  |  | 0
 |  |  |  |  | 0
 |  |  |  |  | 0
 |  |  |  |  | 0
 |  |  |  |  | 0
 |  |  |  |  | 0
 |  |  |  |  | 0
 |  |  |  |  | 0
 |  |  |  |  | 0
 |  |  |  |  | 0
 |  |  |  |  | 0
 |  |  |  |  | 0
 |  |  |  |  | 0
 |  |  |  |  | 0
 |  |  |  |  | 0
 |  |  |  |  | 0
 |  |  |  |  | 0
 |  |  |  |  | 0
 |  |  |  |  | 0
 |  |  |  |  | 0
 |  |  |  |  | 0
 |  |  |  |  | 0
 |  |  |  |  | 0
 |  |  |  |  | 0
 |  |  |  |  | 0
 |  |  |  |  | 0
 |  |  |  |  | 0
 |  |  |  |  | 0
 |  |  |  |  | 0
 |  |  |  |  | 0
 |  |  |  |  | 0
 |  |  |  |  | 0
 |  |  |  |  | 0
 |  |  |  |  | 0
 |  |  |  |  | 0
 |  |  |  |  | 0
 |  |  |  |  | 0
 |  |  |  |  | 0
 |  |  |  |  | 0
 |  |  |  |  | 0
 |  |  |  |  | 0
 |  |  |  |  | 0
 |  |  |  |  | 0
 |  |  |  |  | 0
 |  |  |  |  | 0
 |  |  |  |  | 0
 |  |  |  |  | 0
 |  |  |  |  | 0
 |  |  |  |  | 0

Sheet: PCB BOM
many of the following connectors are standard and can be substituted for altenate methods, ie screw-pins vs headers.
The only connectors that arent standard are the MOLEX / DB9 connectors for motor & encoder IO.
ID | Name | Designator | Footprint | Quantity | Manufacturer Part | Manufacturer | Supplier | Supplier Part | Price
1 | HDR-F-2.54_1x4 | ANALOG_IN,PWMOUT,STEPOUT,MPU9250,ECHO1,ECHO2,ECHO3,ECHO4,ENH1,ENH2,ENH3,ENH4,TEMP1 | HDR-F-2.54_1X4 | 13 |  |  | LCSC | C225501 | 0.07
2 | HDR-F-2.54_1x2 | ES1 | HDR-F-2.54_1X2 | 1 |  |  | LCSC | C49661 | 0.036
3 | MOLEX MINI FIT JR 2x4 8 PIN FEMALE | MOTOR | MOLEX_MINIFIT-JR-5556-08A_2X04X4.20MM_STRAIGHT | 1 |  | Molex
4 | 20k | R6 | R1206 | 1
5 | 100 | R7,R8 | R1206 | 2
6 | 100 | R1,R2,R3,R4,R_MA1 | R0805 | 5
7 | 10k | R5 | R0805 | 1
8 | HDR-F-2.54_1x10 | ADC1 | HDR-F-2.54_1X10 | 1 |  |  | LCSC | C35445 | 0.103
9 | 1u | C1 | CASE-A_3216 | 1
10 | 0.1u | C2 | C0201 | 1
11 | DB9_Female | ENC1,ENC2,ENC3,ENC4 | DSUB-TH_DMR-9S | 4 |  | Ckmtw(灿科盟) | LCSC | C141882 | 0.333
12 | HDR-F-2.54_1x8 | POWER,POWER1 | HDR-F-2.54_1X8 | 2 |  |  | LCSC | C225505 | 0.193
13 | Raspberry Pi GPIO Header | RPI_3.3V,RPI_5V | RASPBERRY_PI_GPIO_HEADER | 2 |  |  |  | undefined
14 | 20k | R_PU1_I2C,R_PU2_I2C | R0805 | 2
15 | 10K | R_PU_HLFB | R0805 | 1
16 | HDR-F-2.54_1x20 | TEST_IO | HDR-F-2.54_1X20 | 1 |  |  | LCSC | C50984 | 0.175

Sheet: Hardware
Wave Tank Material Purchase List |  |  |  |  |  |  | Total Cost | $753.92
Structural Material
Material | Note | Size | Unit | Quantity | Price | Vendors | Link | Cost | STATUS
Non-tempered Glass | safety factor of 2.5 | 1/2'' x 69'' (L) x 21.5'' (W) | Inch | 1 |  | Loca Shop |  |  | pending
Plywood sheets (Hardwood) | pre-sanded, non-treated, furniture grade | 3/4'' x 8' (L) x 4' (W) | Feet | 2 | $80.28 | HomeDepot | https://www.homedepot.com/p/PureBond-3-4-in-x-4-ft-x-8-ft-Poplar-Hardwood-Plywood-5787/317372919 | $160.56 | purchased
Hardwood Square Dowel | 132'' needed (10' x 6; 36'' x 2) | 3/4'' (W) x 3/4'' (H) x 36'' (L) | Inch | 4 | $3.96 | HomeDepot | https://www.homedepot.com/p/Waddell-8312U-3-4-in-x-3-4-in-x-36-in-Hardwood-Square-Dowel-10001817/203334084 | $15.84 | purchased
~~Furring Strip Board~~ | ~~515 1/2" needed (72" x4; 14 3/4" x 10; 20" x 4)~~ | ~~1'' x 96'' (8ft.) (L) x 3'' (W)~~ | ~~Inch~~ | ~~6~~ | ~~$2.48~~ | ~~HomeDepot~~ | https://www.homedepot.com/p/1-in-x-3-in-x-8-ft-Furring-Strip-Board-164704/100094214 | ~~$14.88~~
 |  |  |  |  |  |  |  | $0.00
 |  |  |  |  |  |  |  | $0.00
 |  |  |  |  |  |  |  | $0.00
 |  |  |  |  |  |  | Sub Total | $191.28
Adhesion Material
Material | Note | Size | Unit | Quantity | Price | Vendors | Link | Cost | STATUS
Deck Screw | Coarse Thread Sharp Point Polymer Coated | #8 x 2'' | Inch | 2 | $9.97 | HomeDepot | https://www.homedepot.com/p/Grip-Rite-8-x-2-in-Phillips-Bugle-Head-Coarse-Thread-Sharp-Point-Polymer-Coated-Exterior-Screws-1-lb-Pack-PTN2S1/100197689 | $19.94 | purchased
Wood Gule | Polyurethane Construction Adhesive | 28 oz. | Ounce | 1 | $12.48 | HomeDepot | https://www.homedepot.com/p/Loctite-PL-Premium-28-oz-Polyurethane-Construction-Adhesive-Tan-Cartridge-each-1390594/202020474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 | $12.48 | purchased
Silicone Cement | All-season Aquarium-safe Waterproof | 2.7 oz. | Ounce | 10 | $6.28 | HomeDepot | https://www.homedepot.com/p/Loctite-Silicone-Waterproof-Multipurpose-Adhesive-Sealant-2-7-oz-Clear-Tube-each-908570/303769575 | $62.80 | purchased
Fiberglass Cloth Tape |  | 4'' (W) x 99' (L) | Tap | 1 | $11.99 | Amazon | https://www.amazon.com/Fiberglass-Adhesive-Reinforced-Winding-Molding/dp/B0CBWTM6Q1?s=industrial | $11.99 | purchased
Total Protect Epoxy Barrier Coat Primer | 28 sq ft. needed | 1 gal. (225 sq ft) | Gallon | 1 | $124.99 | TotalBoat | https://www.totalboat.com/products/totalprotect-epoxy-barrier-coat-primer?variant=43148111773920 | $124.99 | purchased
Epoxy Primer Thinner 200 |  | 1 qt. (0.25 gal,) | Quart | 1 | 26.99 | TotalBoat | https://www.totalboat.com/products/epoxy-primer-thinner-200-solvent | $26.99 | purchased
Wet Edge Topside Paint | Navy Bule | 1 gal. (225 sq ft) | Gallon | 1 | 124.99 | TotalBoat | https://www.totalboat.com/products/wet-edge-marine-topside-paint | $124.99 | not needed
 |  |  |  |  |  |  | Sub Total | $384.18
Electronic Instrument
Material | Note | Size | Unit | Quantity | Price | Vendors | Link | Cost | STATUS
Reciprocating Linear Actuator Kit Motor | High Torque 40 lbs | 24V150mm120rpm | Set | 1 | $117.99 | Amazon | https://www.amazon.com/JQDML-Reciprocating-Regulator-Connector-12V150mm95rpm/dp/B095HCVNZC | $117.99
Gyroscope Acceleration Magnetic Sensor |  |  |  | 1 | $14.99 | Amazon | https://www.amazon.com/HiLetgo-Gyroscope-Acceleration-Accelerator-Magnetometer/dp/B01I1J0Z7Y?s=industrial | $14.99
Injection Molding Electronic Ruler Pull Rod Displacement Sensor |  |  |  | 1 | 35.49 | Amazon | https://www.amazon.com/Injection-Electronic-Displacement-Protection-Stainless/dp/B08BZNV7Q3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 | $35.49
Encoder Magnetic Induction Angle Measurement Sensor |  | 23mm x 23mm (0.91‘’x0.91‘’) | 3pcs | 1 | 9.99 | Amazon | https://www.amazon.com/Magnetic-Encoder-Induction-Measurement-Precision/dp/B094F8H591?th=1 | $9.99
Tension and Compression Load Cell |  |  |  |  | 137.98 | ATO | https://www.ato.com/tension-and-compression-load-cell-1kg-to-200kg?affiliate=shopping&gad_source=1 | $0.00
 |  |  |  |  |  |  |  | $0.00
 |  |  |  |  |  |  |  | $0.00
 |  |  |  |  |  |  | Sub Total | $178.46
Tools
Name | Note | Size | Unit | Quantity | Price | Vendors | Link | Cost | STATUS
Medium and Large Trigger Clamp | 2 set more |  | Pack | 1 | 36.97 | HomeDepot | https://www.homedepot.com/p/DEWALT-Medium-and-Large-Trigger-Clamp-4-Pack-DWHT83196/205086878 | $36.97 | purchased
90-Degree Right Angle Corner Assembly Clamp Squares |  | 4" & 8" (8pcs) | Kit | 1 | 34.99 | HomeDepot | https://www.homedepot.com/p/Milescraft-8-in-and-4-in-Squares-Corner-Square-Kit-90-Degree-Right-Angle-Corner-Assembly-Clamp-Squares-8-Piece-7366/319854770 | $34.99 | purchased
Laser Etched Aluminum Rafter Square |  |  |  | 1 | 13.97 | HomeDepot | https://www.homedepot.com/p/Empire-7-in-Laser-Etched-Aluminum-Rafter-Square-e2994/205317688 | $13.97 | not needed
Spring Clamp Set |  | 22 pcs | Set | 1 | 9.97 | HomeDepot | https://www.homedepot.com/p/Anvil-Spring-Clamp-Set-22-Piece-TGS0199A/302755768 | $9.97 | not needed

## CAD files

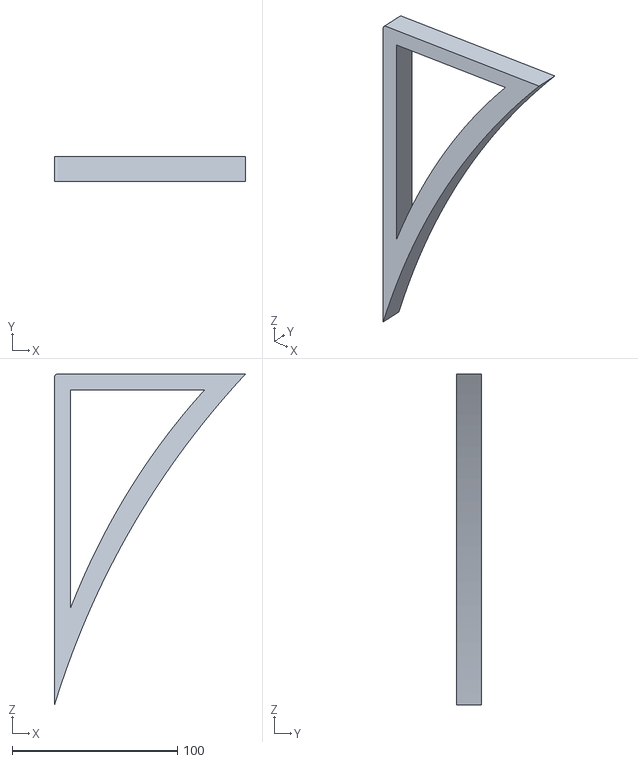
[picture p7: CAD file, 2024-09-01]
design_files/cad & schematics/3D print/spool1 - paddle-test1.stl
115.5 x 15.0 x 200.0

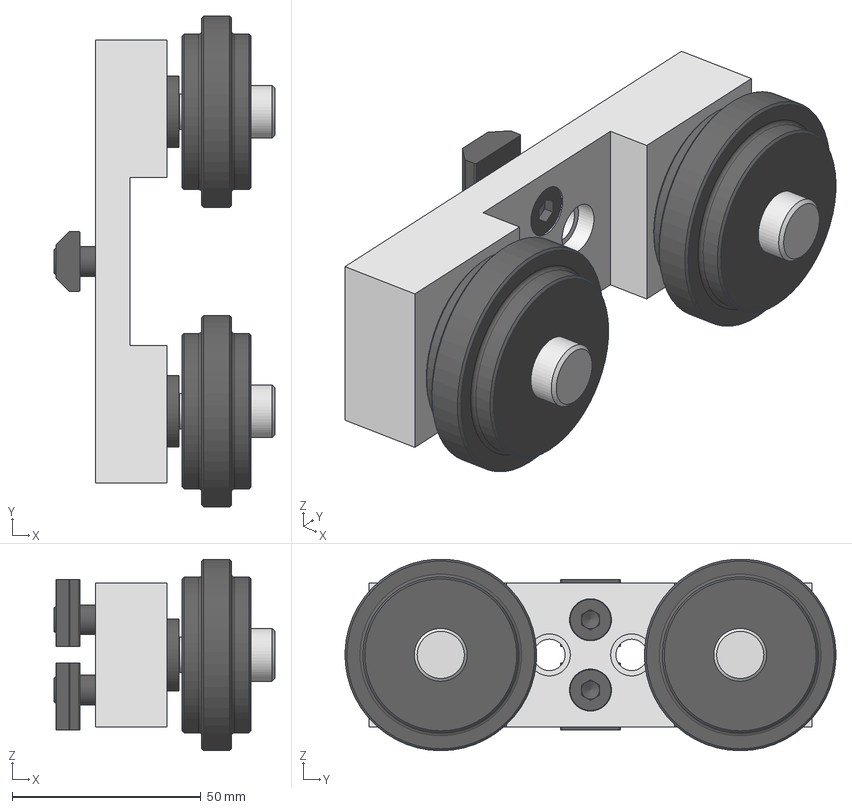
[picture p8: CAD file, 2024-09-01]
design_files/cad & schematics/8020_27561/2756-1.stp
58.6 x 130.2 x 50.8 mm
2754-1_b
2290_b x 2
2290_w x 2
2290_p2 x 2

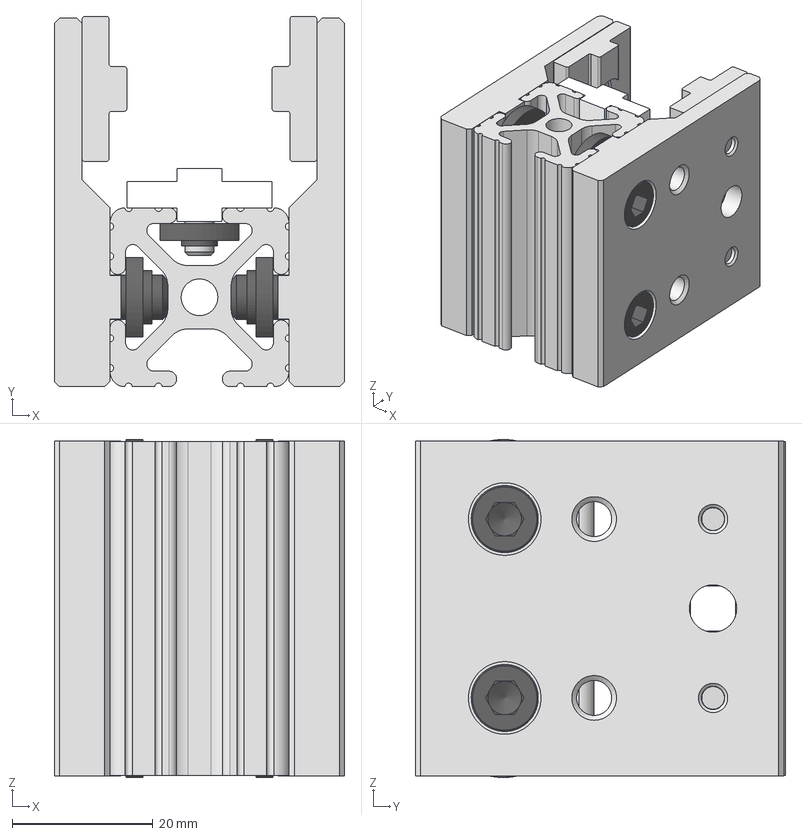
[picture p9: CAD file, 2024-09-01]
design_files/cad & schematics/8020_6730/6730.stp
41.2 x 52.6 x 48.0 mm
1010-1.87-CL
6760_p x 2
6705_p x 2
6792_p
FHSCS-8-32 x 2

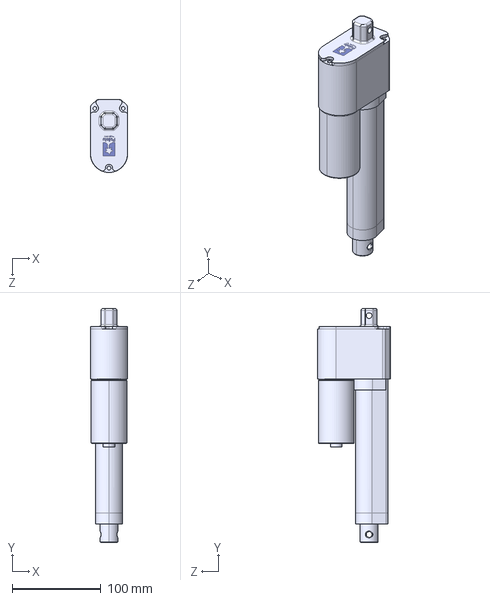
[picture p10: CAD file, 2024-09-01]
design_files/cad & schematics/Glideforce-LD-3d-models/Glideforce-LD-LACT4P.step
42.0 x 263.0 x 82.0 mm
aluminum-frame_4in with pot
extension-tube_4in frame

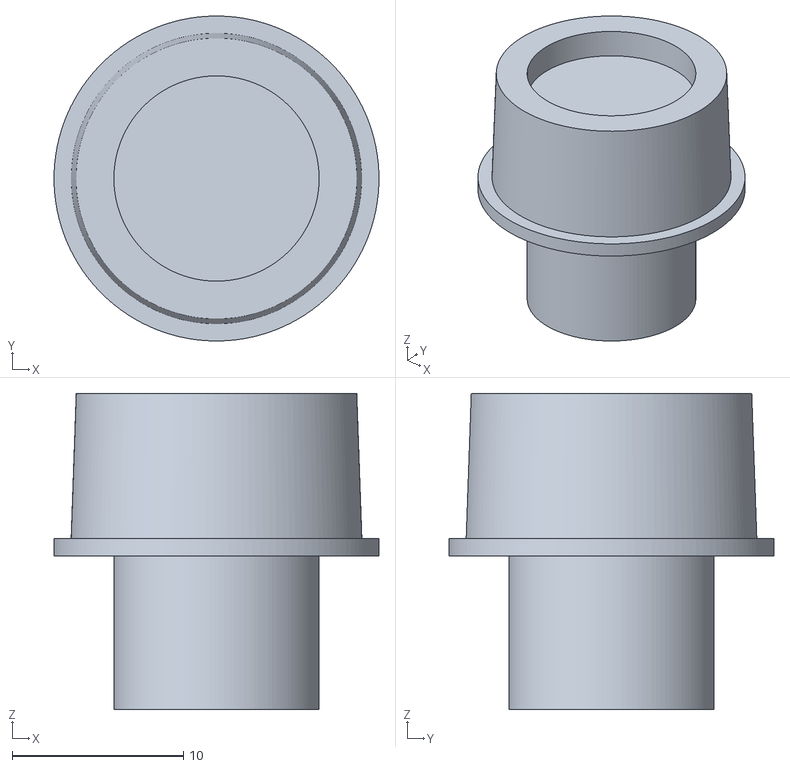
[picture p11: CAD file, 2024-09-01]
design_files/cad & schematics/3D print/motor cap.stl
19.0 x 19.0 x 18.5

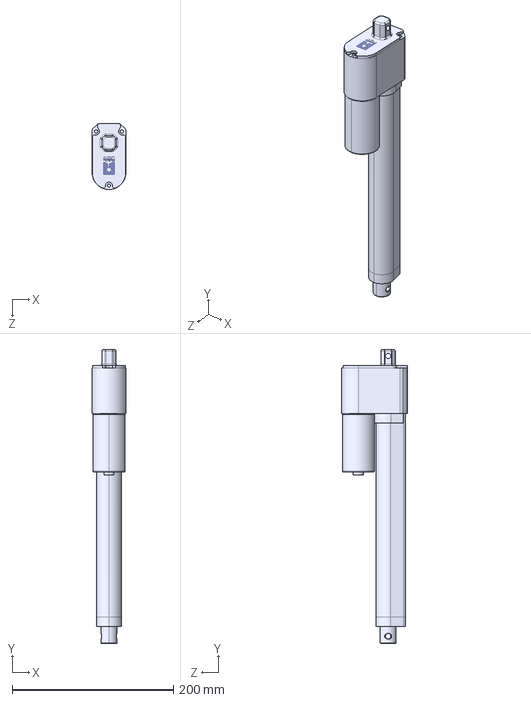
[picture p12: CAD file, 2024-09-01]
design_files/cad & schematics/Glideforce-LD-3d-models/Glideforce-LD-LACT8P.step
42.0 x 365.0 x 82.0 mm
aluminum-frame_8in with pot
extension-tube_8in frame

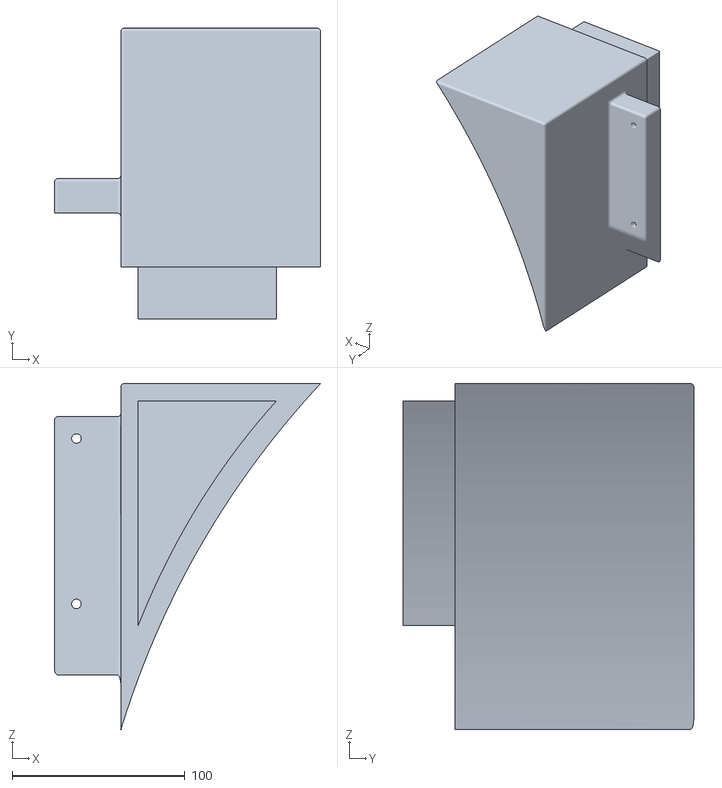
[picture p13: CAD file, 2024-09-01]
design_files/cad & schematics/3D print/paddle3.stl
153.8 x 168.0 x 200.0

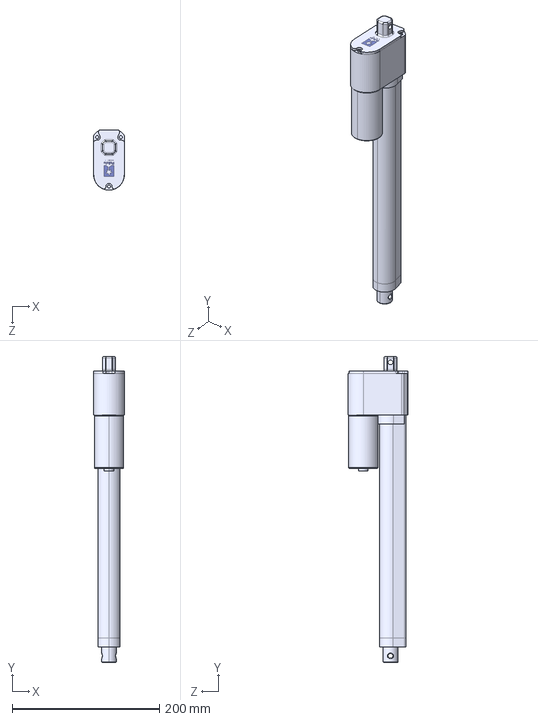
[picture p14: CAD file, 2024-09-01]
design_files/cad & schematics/Glideforce-LD-3d-models/Glideforce-LD-LACT10P.step
42.0 x 416.0 x 82.0 mm
aluminum-frame_10in with pot
extension-tube_10in frame

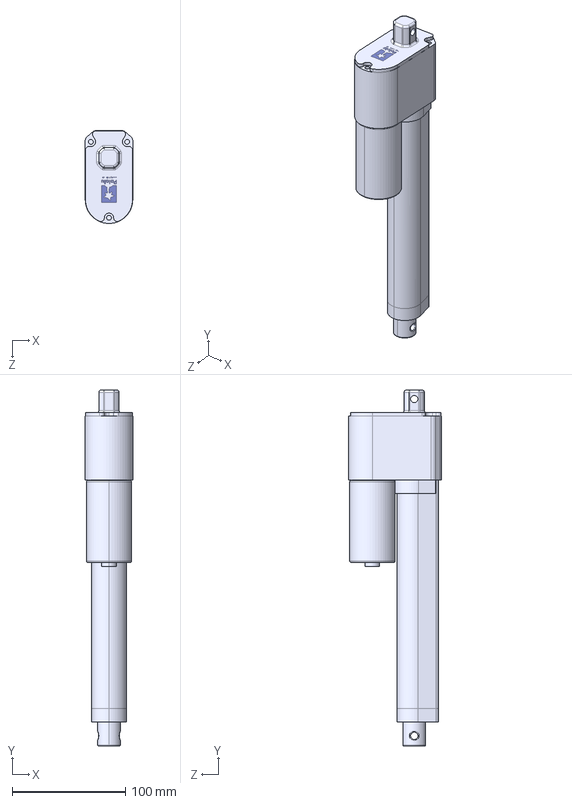
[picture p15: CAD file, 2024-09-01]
design_files/cad & schematics/Glideforce-LD-3d-models/Glideforce-LD-LACT6P.step
42.0 x 314.0 x 82.0 mm
aluminum-frame_6in with pot
extension-tube_6in frame

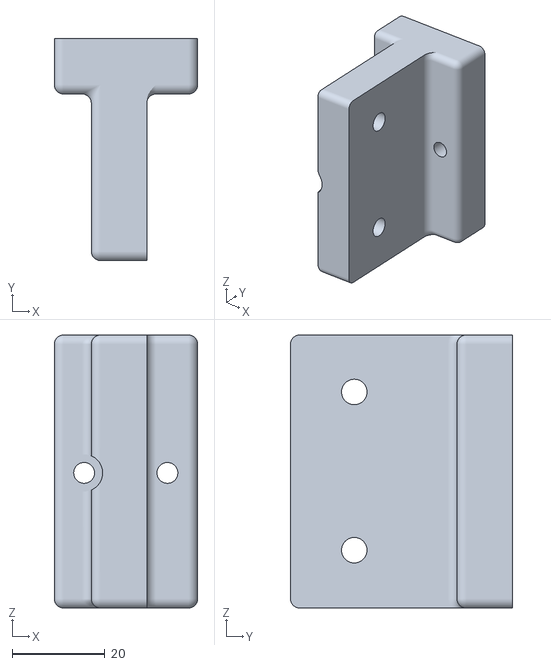
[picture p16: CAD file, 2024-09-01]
design_files/cad & schematics/3D print/spool1 x2 - traveller.stl
31.0 x 48.0 x 59.0

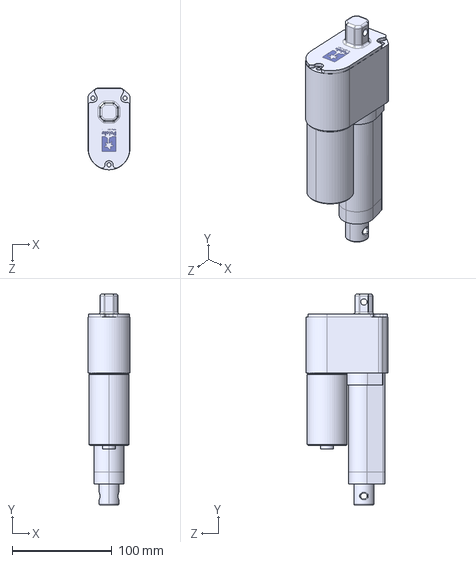
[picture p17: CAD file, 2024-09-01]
design_files/cad & schematics/Glideforce-LD-3d-models/Glideforce-LD-LACT2P.step
42.0 x 212.0 x 82.0 mm
aluminum-frame_2in with pot
extension-tube_2in frame

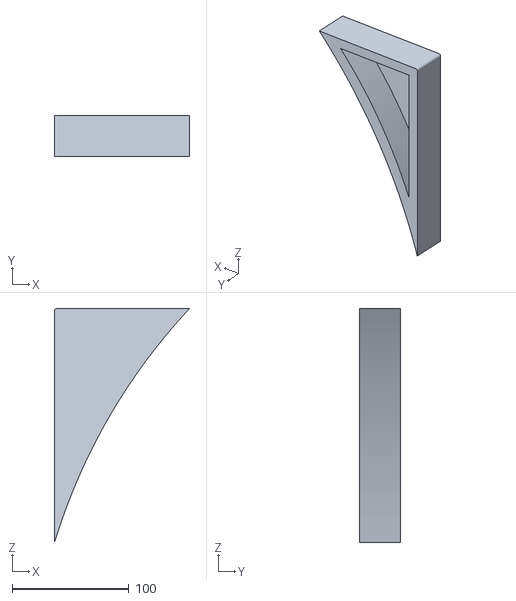
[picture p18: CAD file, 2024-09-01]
design_files/cad & schematics/3D print/paddle-test2.stl
115.5 x 35.2 x 200.0

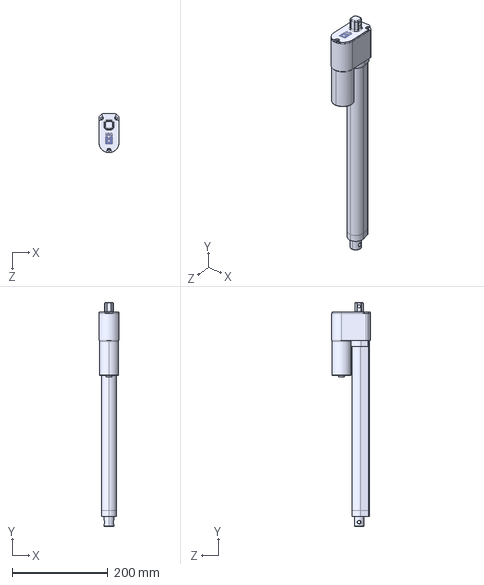
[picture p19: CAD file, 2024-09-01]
design_files/cad & schematics/Glideforce-LD-3d-models/Glideforce-LD-LACT12P.step
42.0 x 467.0 x 82.0 mm
aluminum-frame_12in with pot
extension-tube_12in frame

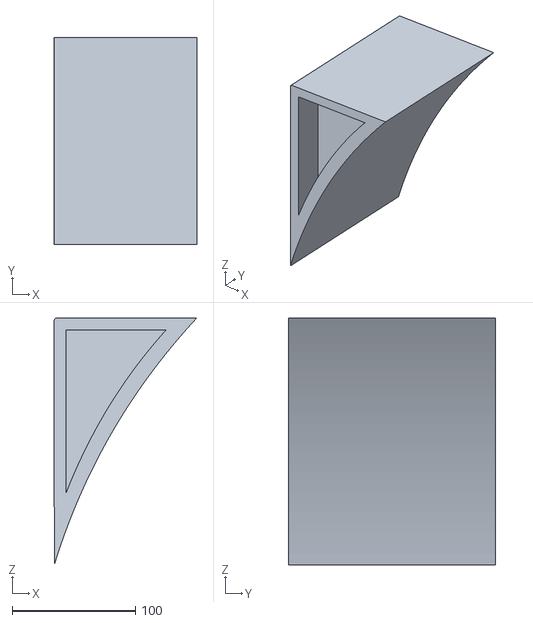
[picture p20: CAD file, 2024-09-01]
design_files/cad & schematics/3D print/paddle2.stl
115.5 x 168.0 x 200.0

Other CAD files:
design_files/cad & schematics/3D print/spool1 - paddle1.stl

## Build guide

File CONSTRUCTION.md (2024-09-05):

# Overview & 3D Model

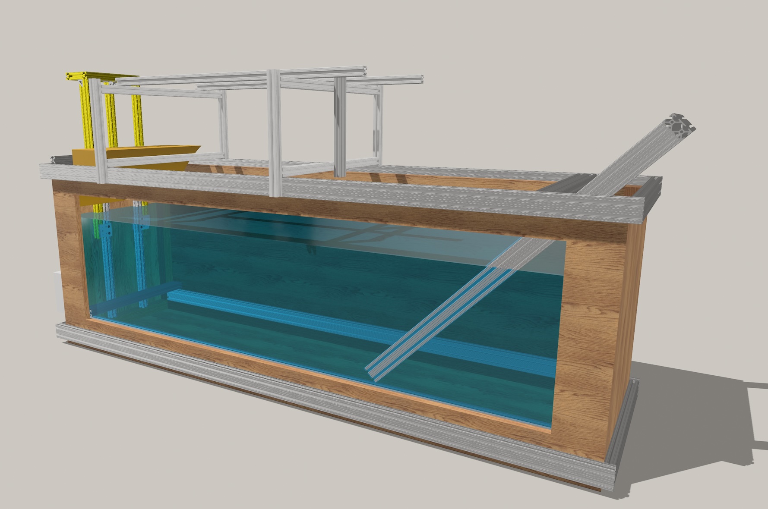
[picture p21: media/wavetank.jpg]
Wave Tank 3D model


### 3D visualization: [3D viewer](https://collaborate.shapr3d.com/v/NPVw5xXpwtwc81BRGQEVF)

### 3D models: inside [CAD & Schematics](https://github.com/neptunyalabs/wavetankOS/tree/main/design_files/cad%20%26%20schematics) folder, feel free to inspect and study its construction

# Tank Construction Sequence
## 1. Wood Work
- Start by purchasing wood material and supplies described in the BOM files, under [design_files](https://github.com/neptunyalabs/wavetankOS/tree/main/design_files) folder
- Cut wood panels as laid out in 3D model file, under [CAD & Schematics](https://github.com/neptunyalabs/wavetankOS/tree/main/design_files/cad%20%26%20schematics) folder
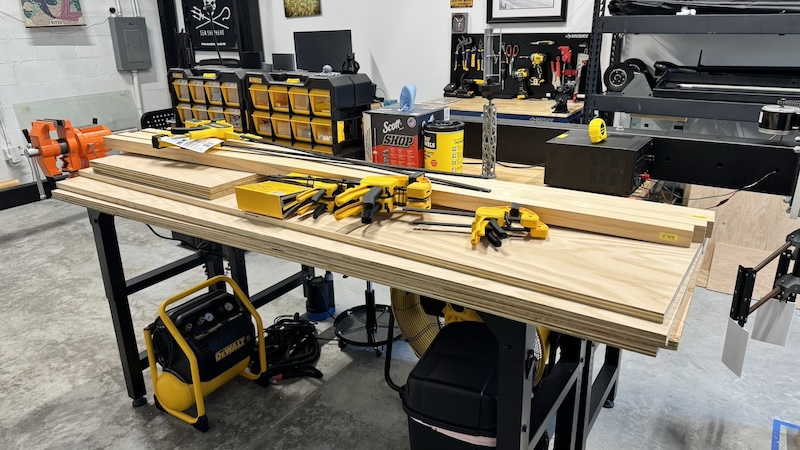
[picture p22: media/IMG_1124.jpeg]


- Using Construction Adhesive glue wood panel corners to a hardwood square dowel
- Use 90 degree clamps to hold them in place
- Mark and insert wood deck screws, aligned on every 2 inches, pre-drill to avoid future cracks
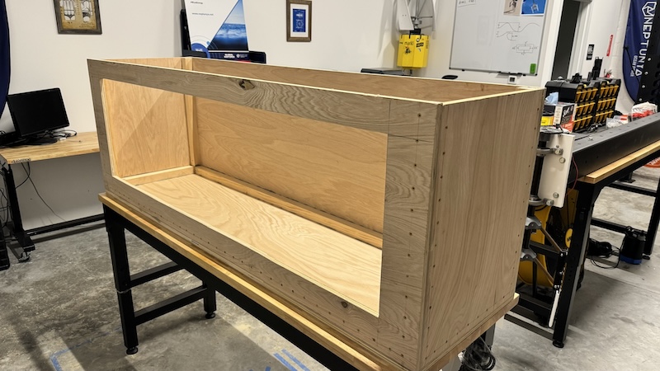
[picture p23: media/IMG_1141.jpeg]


## 2. Water Proofing
- Sand wood panels and mask tank edges
- Mix epoxy paint and hardener
- Paint the tank inside with waterproof epoxy paint
- Use fiberglass cloth over tank corners
> [!CAUTION]
> Perform waterproofing work on a well ventilated area
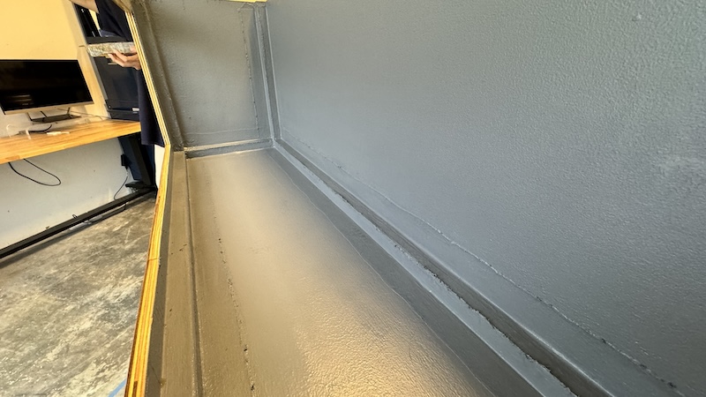
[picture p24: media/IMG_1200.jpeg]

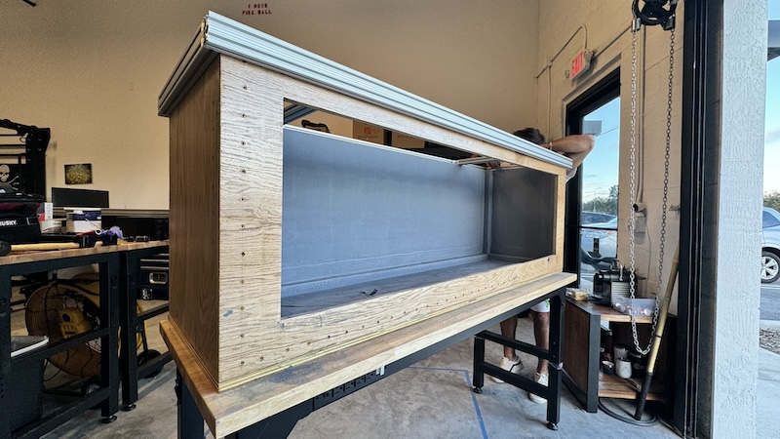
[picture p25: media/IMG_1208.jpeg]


## 3. Window Install
- Using Construction Adhesive glue acrylic window to wood frame
- Use wood clamps to hold it in place while curing adhesive
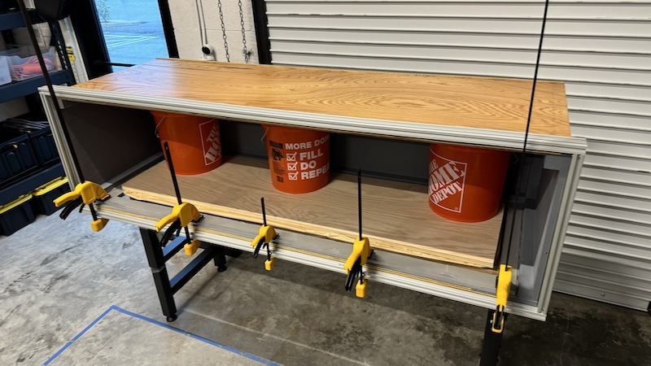
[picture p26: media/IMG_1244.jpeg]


- Seal window edges with high-grade silicone calk
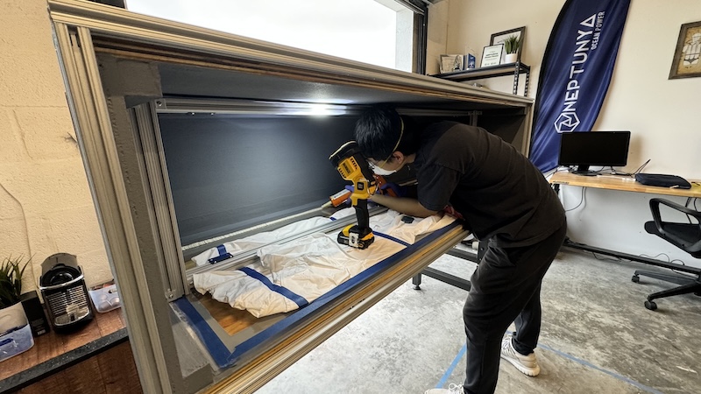
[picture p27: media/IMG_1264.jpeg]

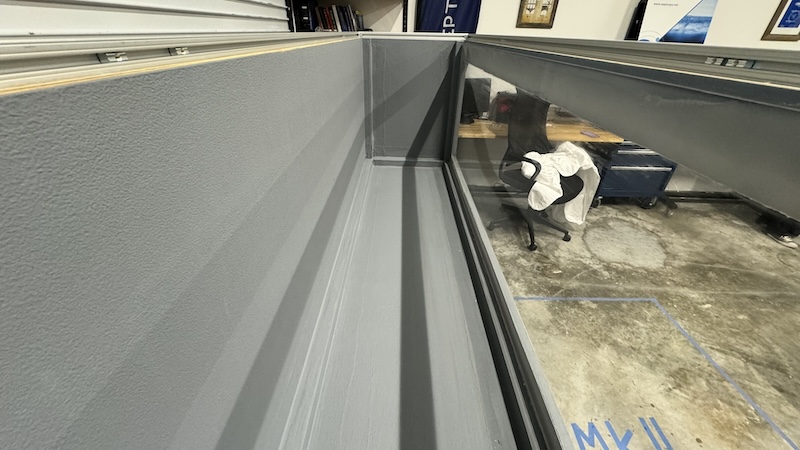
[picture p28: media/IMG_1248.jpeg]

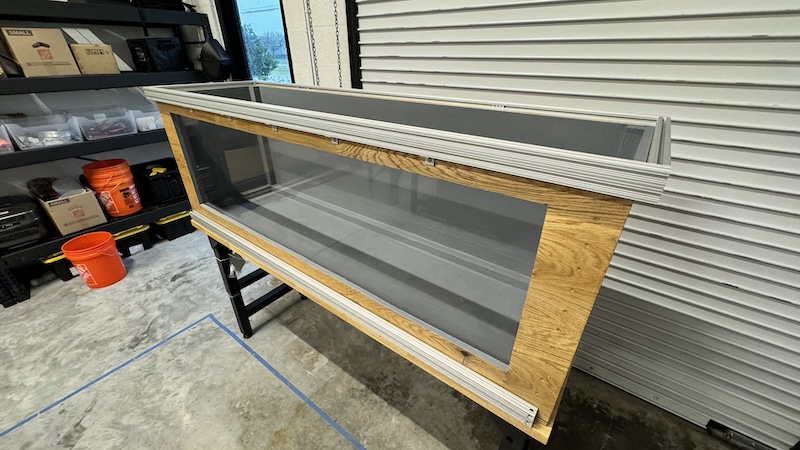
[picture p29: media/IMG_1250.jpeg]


## 4. 8020 Frame
- Pre-drill and attach 8020 aluminum frame with SS wood screws
- Start from the base frame, then attach upper supports
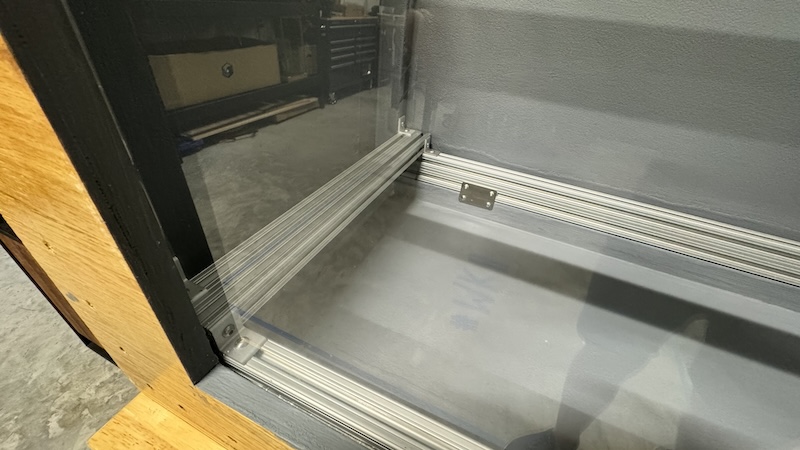
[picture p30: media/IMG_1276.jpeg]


- Finish installing external 8020 frame, top & bottom
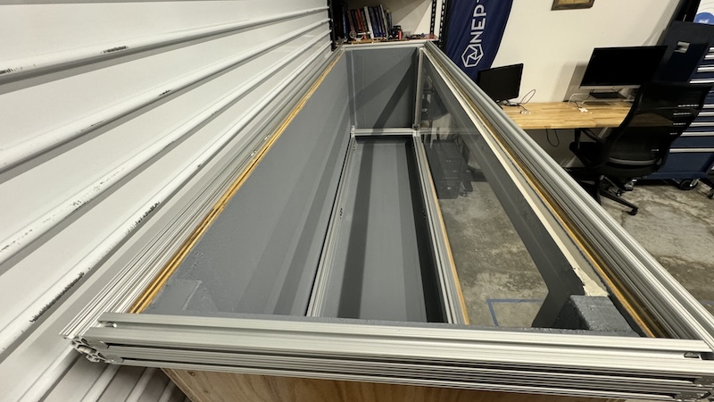
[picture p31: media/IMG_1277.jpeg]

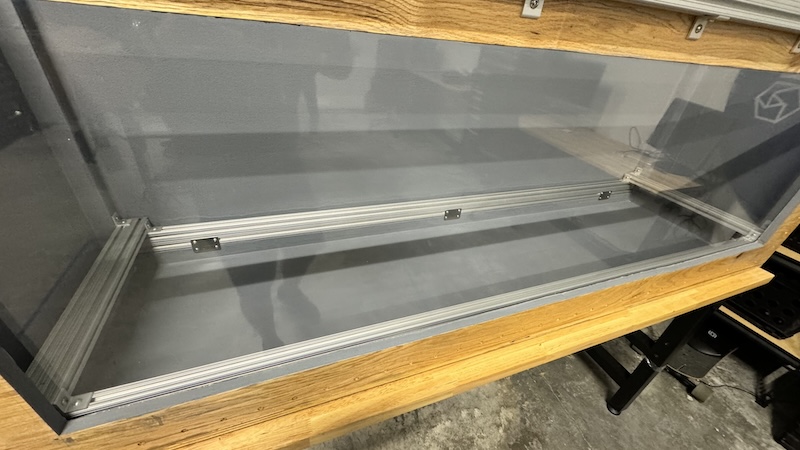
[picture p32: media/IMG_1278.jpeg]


## 5. Water Test (wait at least 48h to fully cure)
- Now it's time to the first water test
- Fill-up the tank with water and inspect for issues at every stage
- Make some water movement tests
- Inspect the tank surroundings for any sign of leak
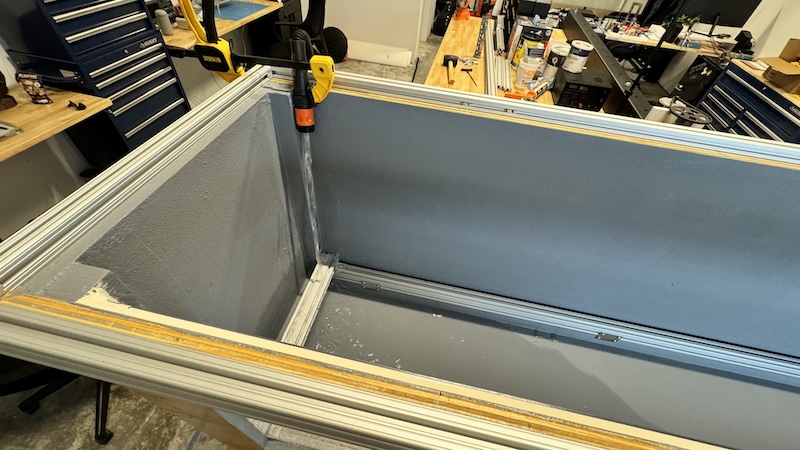
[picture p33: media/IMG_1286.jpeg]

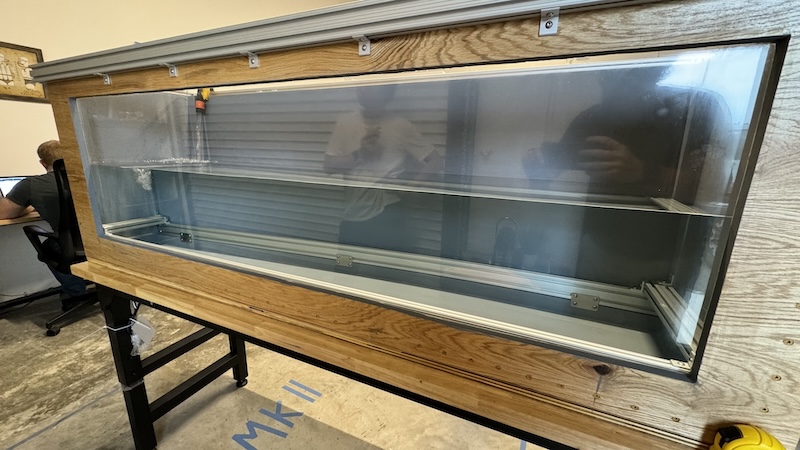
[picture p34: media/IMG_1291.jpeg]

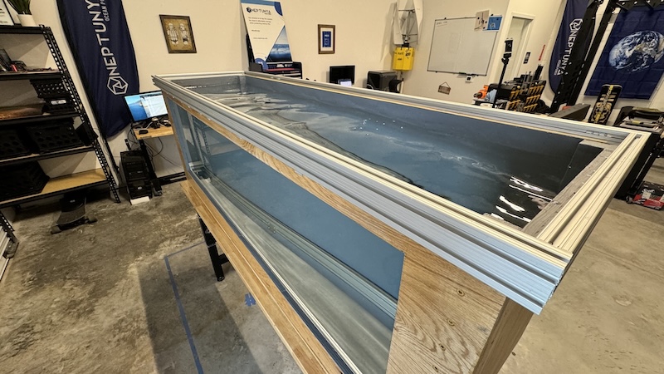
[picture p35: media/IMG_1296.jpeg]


# Final Product
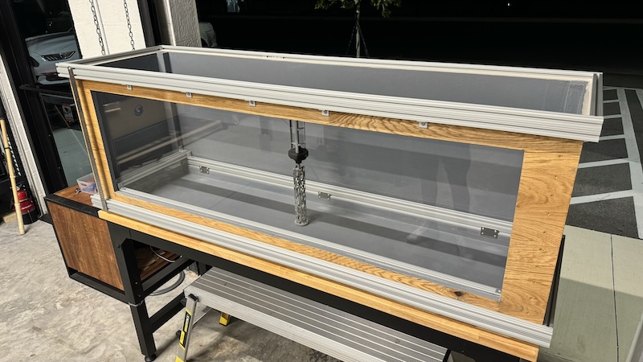
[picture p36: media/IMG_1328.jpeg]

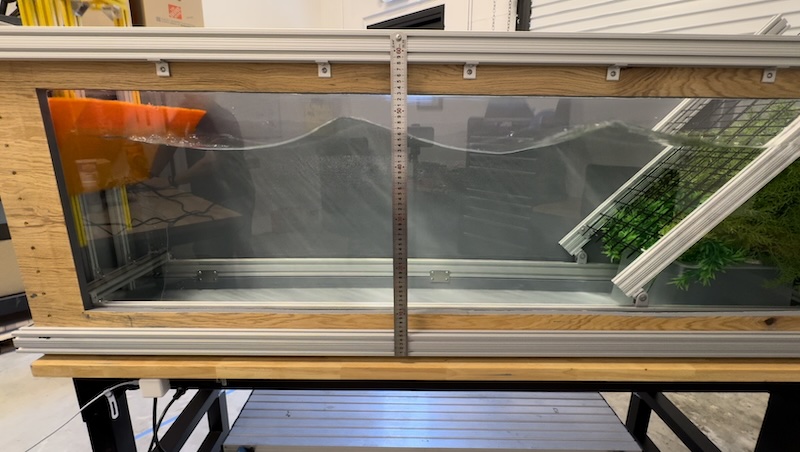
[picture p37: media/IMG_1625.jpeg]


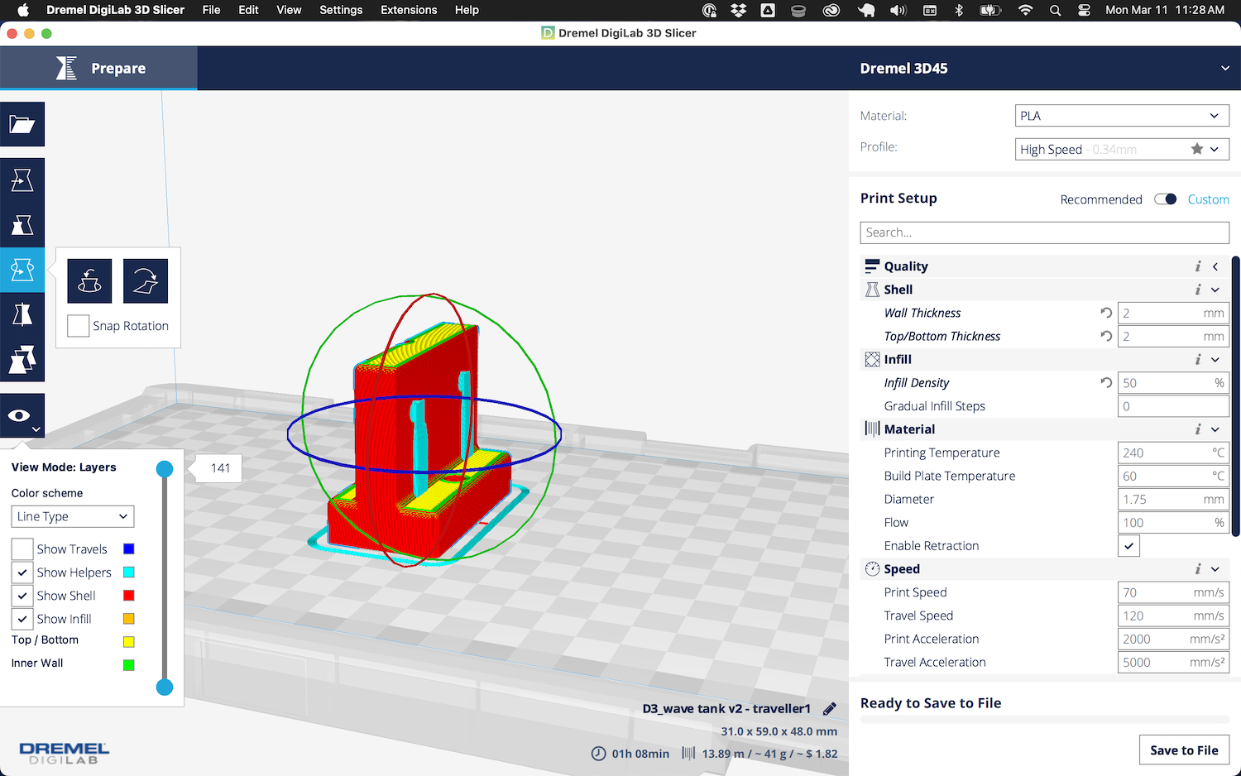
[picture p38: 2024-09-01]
design_files/cad & schematics/3D print/spool1 x2 - traveller.png

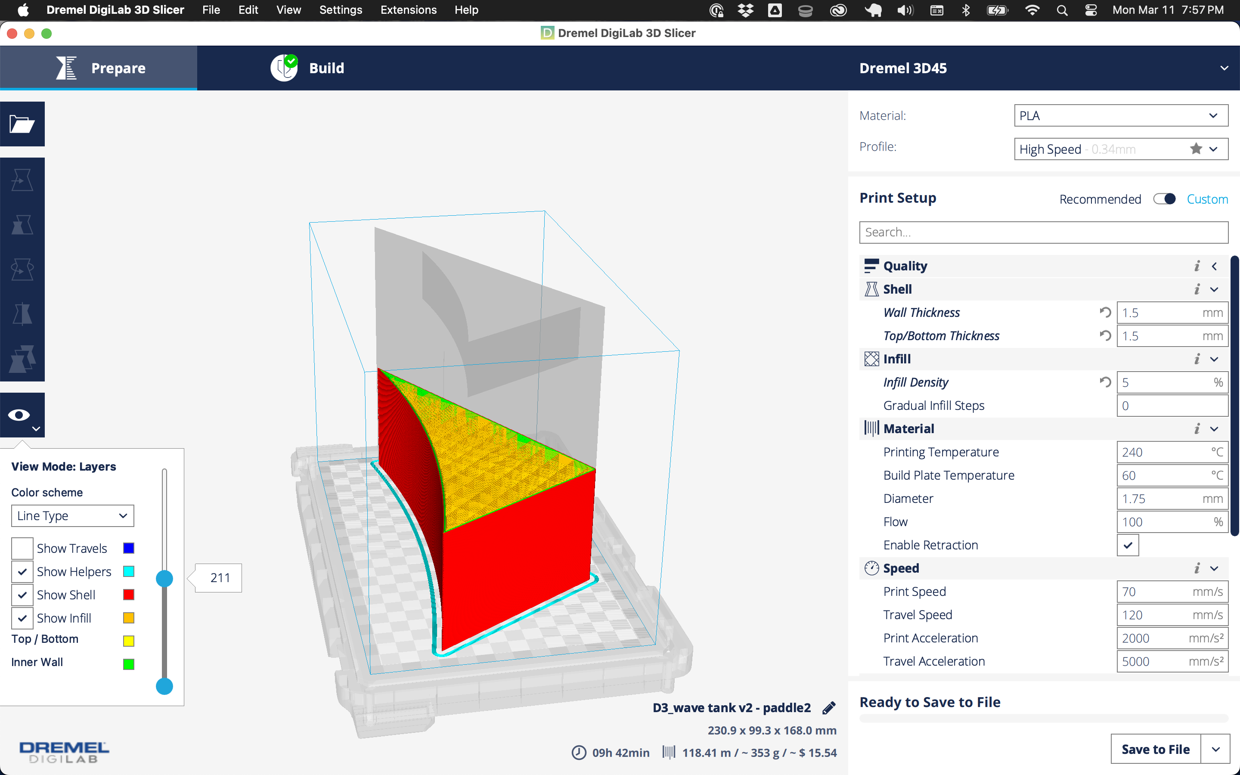
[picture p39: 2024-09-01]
design_files/cad & schematics/3D print/paddle2.png

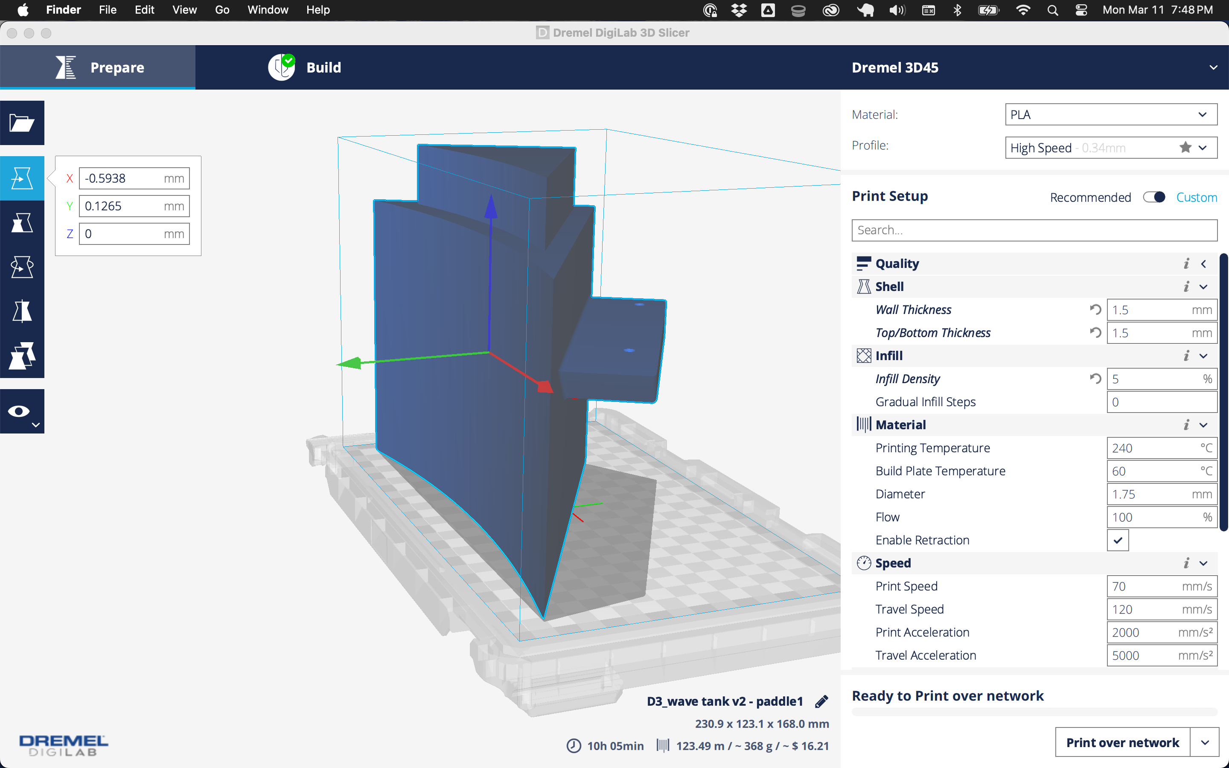
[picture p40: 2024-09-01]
design_files/cad & schematics/3D print/spool1 - paddle1.png

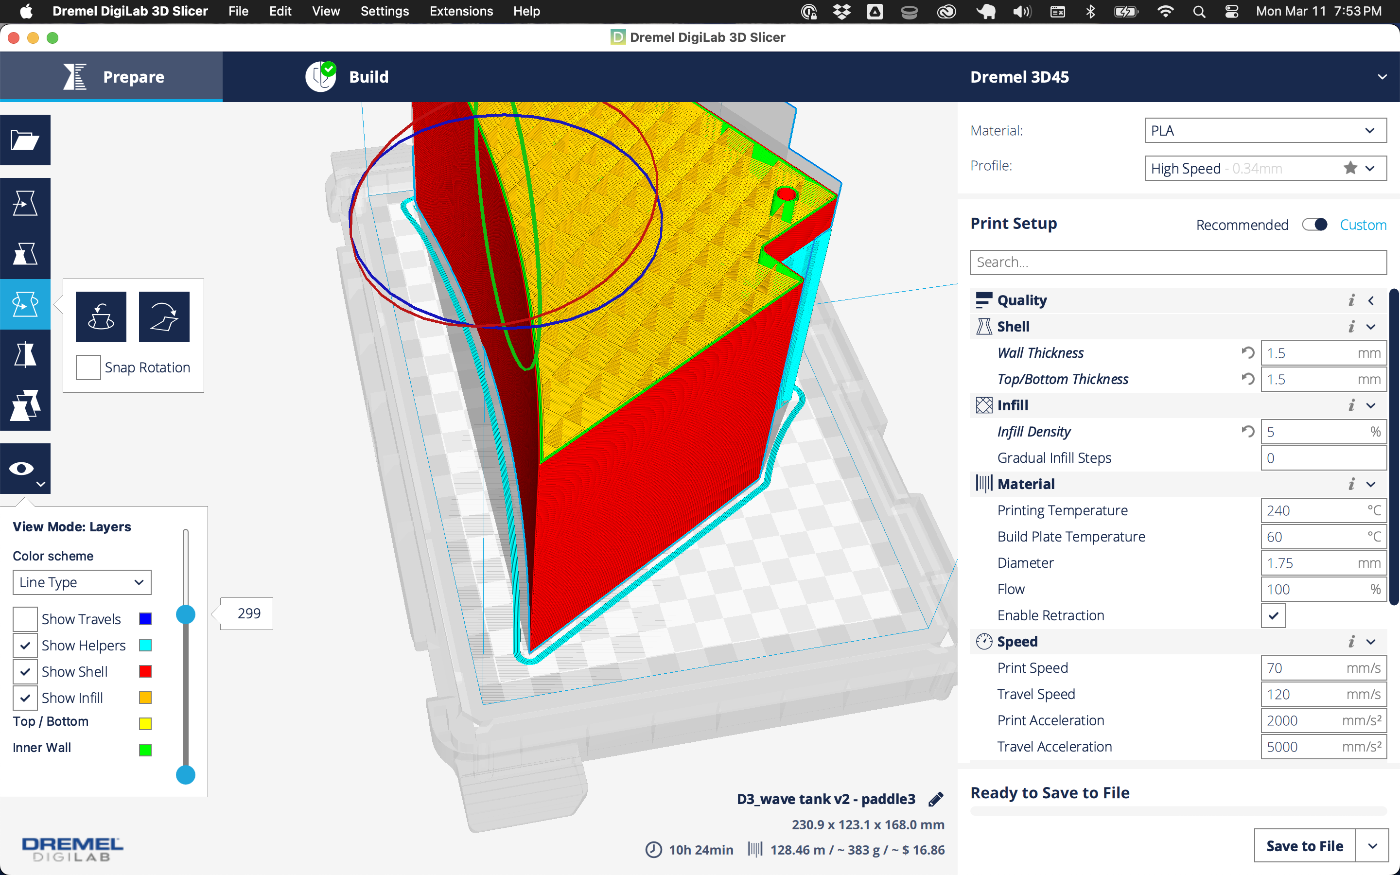
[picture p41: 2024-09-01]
design_files/cad & schematics/3D print/paddle3.png

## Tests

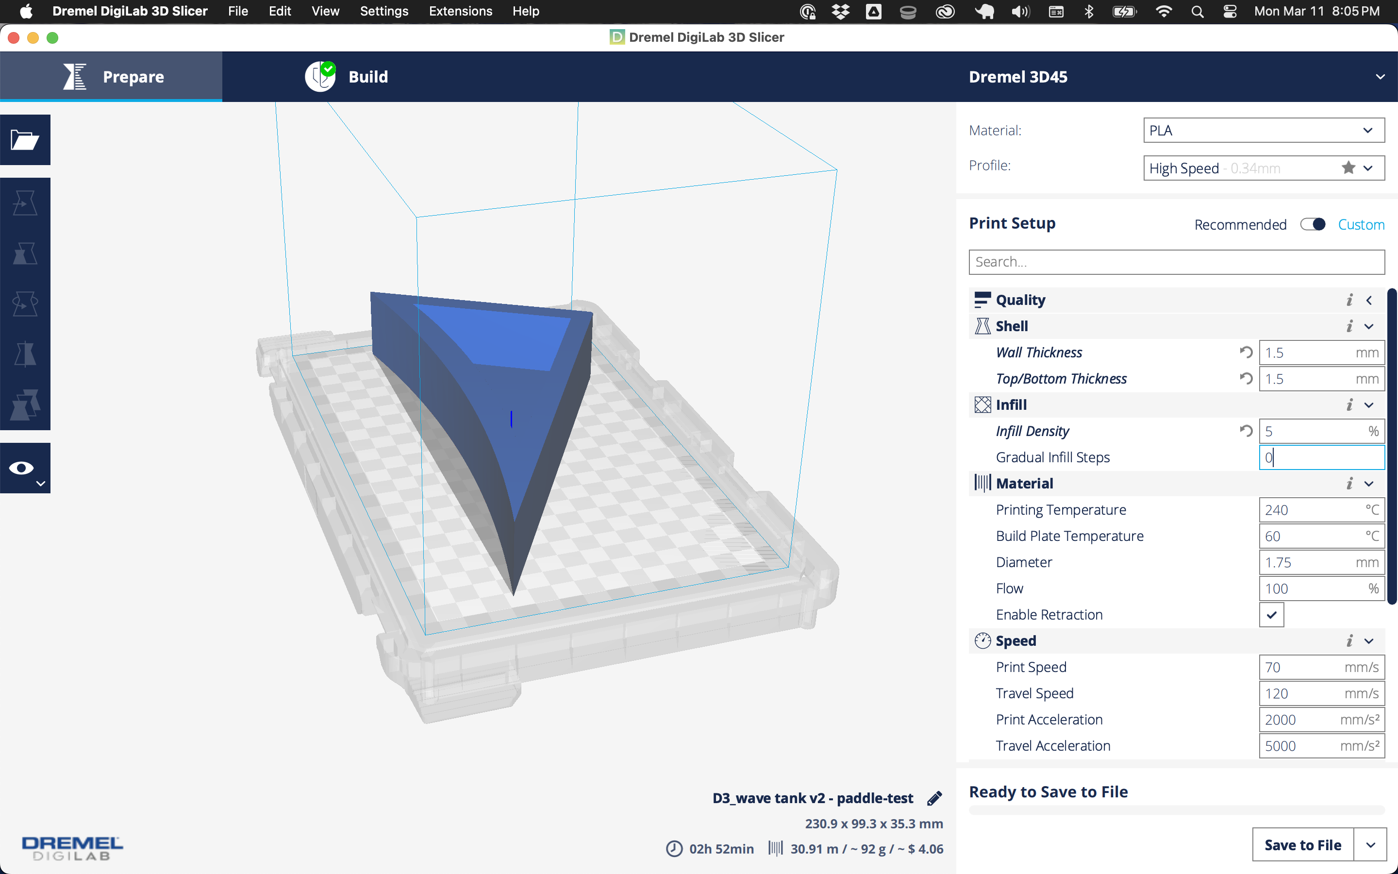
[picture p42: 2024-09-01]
design_files/cad & schematics/3D print/paddle-test2.png

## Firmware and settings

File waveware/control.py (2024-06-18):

"""
in which we define motion classes
1. stepper_control: class provides a stepper control based off step/dir concept #TODO
2. motion_control: class provides a high level PWM based interface for speed/torque with position control #TODO
"""
import asyncpio
import asyncio
import time
import traceback
import signal

import json
import threading
import time
import sys,os,pathlib
import math
from waveware.config import *
from waveware.data import *
import random

# Get I2C bus

log = logging.getLogger('cntl')


control_dir = pathlib.Path(__file__).parent

class MovementError(Exception): pass
class StuckError(MovementError): pass
class NoMotion(MovementError): pass



#ADC stuff
p_adc = {0:'100',1:'101',2:'110',3:'111'}
fv_ref = {6:'000',4:'001',2:'010',1:'011'}
volt_ref = {6:6.144,4:4.096,2:2.048,1:1.024}
dr_ref = {8:'000',16:'001',32:'010',64:'011',128:'100',250:'101',475:'110',860:'111'}

def config_bit(pinx,fvinx=4):
    dv = p_adc[pinx]
    vr = fv_ref[fvinx]
    return int(f'1{dv}{vr}0',2)

wait_factor = 2
fv_inx = 4
dr_inx = 128#860
dr = dr_ref[dr_inx]
min_res = volt_ref[fv_inx]/(2**16/2)
# see https://thecavepearlproject.org/2020/05/21/using-the-ads1115-in-continuous-mode-for-burst-sampling/
low_thres = 0x0000 
high_thres = 0x8000


vmove=vmove_default=[0.0001,0.001]

PR_INT = 1000
    
steps_per_rot = 360/1.8
dz_per_rot = 0.01 #rate commad

class wave_control:
    enabled = False
    wave: regular_wave
    control_interval: float = 10./1000 #valid on linux, windows is 15ms

    kp_zerr = 0.0
    ki_zerr = 0.0
    kd_zerr = 0.0

    
    min_dt = 25
    pulse_dt = 100
    dz_range = 0.3 #meters #TODO: input actual length of lead screw

    adc_addr = 0x48
    t_command = 0 #torque fraction of upper limit 0-1

    def __init__(self, dir:int,step:int,speed_pwm:int,fb_an_pin:int,hlfb:int,torque_pwm,motor_en_pin,pi=None,**conf):
        """This class represents an A4988 stepper motor driver.  It uses two output pins
        
        for direction and step control signals."""
        #setup drive mode first
        self.drive_mode = 'stop'
        self.mode_changed = asyncio.Future()
        self.set_mode('stop')# #always start in calibration mode

        self.force_cal =  conf.get('force_cal',False)
        self.wave = conf.get('wave',regular_wave())
        self.steps_per_rot = conf.get('steps_per_rot',steps_per_rot)
        self.dz_per_rot = conf.get('dz_per_rot',dz_per_rot)
        #self.on_time_us = 25 #us
        self.dz_per_step = self.dz_per_rot / self.steps_per_rot


        self.max_speed_motor = 0.5 #TODO: get better motor constants
                
        self.stopped = True
        self._motor_en_pin = motor_en_pin
        self._dir_pin = dir
        self._step_pin = step
        self._vpwm_pin = speed_pwm
        self._tpwm_pin = torque_pwm
        self._adc_feedback_pin = fb_an_pin
        self._hlfb = hlfb

        self.dt_sc = 0.005
        self.pwm_speed_base = 1000
        self.pwm_speed_freq = 500        
        
        #TODO: setup high/low interrupt on hlfb for ppr or torque / speed ect

        #setup pi if one isn't provided
        #FIXME; cant print un-connected pi
        if pi is None:
            pi = asyncpio.pi()
            log.info(f'control making pi: {type(pi)}|{id(pi)}')
            self.pi = pi
        else:
            log.info(f'adding pi: {type(pi)}|{id(pi)}')
            self.pi = pi

        self.reset()

        
    
    def reset(self):
        #fail setupso
        self.last_print = 0

        self.enabled = False
        self._control_modes = {}
        self._control_mode_fail_parms = {'stop':False,
                                        'center':False,
                                        'cal':False,
                                        'wave':False}

        self.speed_control_mode = default_speed_mode
        self.mode_changed = None
        self.speed_control_mode_changed = None
        self.first_feedback = None

        self._last_dir = 1
        self.feedback_volts = 0
        self.last_feedback = 0
        self.fail_feedback = None

        self.fail_st = False
        self.fail_sc = False
        self.v_cmd =v= 0
        self.v_cur =v= 0
        self.v_sup = 0
        self.v_wave = 0
        self.z_cur = 0
        self.z_wave = 0
        self.z_err = 0        

        self.wave_last = None
        self.wave_next = None

        #TODO: redo calibration system
        c0 = -0.0001

        self.err_int = 0
        self.dt = 0
        self.inx = 0
        self.coef_2 = c0
        self.coef_10 = c0
        self.coef_100 = c0
        self._coef_2 = c0
        self._coef_10 = c0
        self._coef_100 = c0        
        self.dvdt_2 = 0
        self.dvdt_10 = 0
        self.dvdt_100 = 0

        tol = 0.25
        self.v_active_tol = 0.1
        self.act_max_speed = LABEL_DEFAULT['vz-max']
        
        self.v_max = 3.3
        self.v_min = 0
        self.zero_frac = 0.5
        self.lower_frac = 0.33
        self.upper_frac = 0.66
        self.upper_v = self.v_max - tol
        self.lower_v = tol
        self.vref_0 = (self.upper_v + self.lower_v)*self.zero_frac
        self.z_center = self.dz_range*self.zero_frac

        self.update_const()  

    #SETUP 
    async def _setup(self):


        if ON_RASPI:
            if not hasattr(self,'pi') or not isinstance(self.pi,asyncpio.pi):
                log.info(f'making pi last sec')
                self.pi = asyncpio.pi()
            if not hasattr(self.pi,'connected'):
                con = await self.pi.connect()
                self.pi.connected = True
                log.info(f'PI Connection Res: {con}')

            await self.pi.set_mode(self._motor_en_pin,asyncpio.OUTPUT)
            await self.pi.set_mode(self._dir_pin,asyncpio.OUTPUT)
            await self.pi.set_mode(self._step_pin,asyncpio.OUTPUT)
            await self.pi.set_mode(self._tpwm_pin,asyncpio.OUTPUT)
            await self.pi.set_mode(self._vpwm_pin,asyncpio.OUTPUT)

            await self.pi.set_mode(self._hlfb,asyncpio.INPUT)
            await self.pi.set_mode(self._adc_feedback_pin,asyncpio.INPUT)

            await self.pi.write(self._motor_en_pin,0)
            await self.pi.write(self._dir_pin,0)
            await self.pi.write(self._step_pin,0)
            await self.pi.write(self._tpwm_pin,0)
            await self.pi.write(self._vpwm_pin,0)
            log.info(f'raspi setup!')   

    def mark_start(self):
        self.start = time.perf_counter()
        self.start_dt = datetime.datetime.now(tz=pytz.utc)

    def setup(self,i2c=False,cntl=False):
        self.mark_start()
        loop = asyncio.get_event_loop()

        self.feedback_task = loop.create_task(self.feedback())
        self.feedback_task.add_done_callback(check_failure('feedbck task'))

        if i2c:
            self.setup_i2c()

        if cntl:
            #requires i2c, but that can be set in outer fw
            self.setup_control()            

        self.speed_control_mode = default_speed_mode

        self.mode_changed = asyncio.Future()
        self.speed_control_mode_changed = asyncio.Future()    

        loop.run_until_complete(self._setup())    

    def set_speed_tasks(self):
        #SPEED CONTROL MODES
        loop = asyncio.get_event_loop()
        self.mark_start()
        
        
        if DEBUG: log.info(f'set tasks ex feedback / speed / pwm & steps')

        self.speed_off_task = loop.create_task(self.speed_control_off())
        self.speed_off_task.add_done_callback(check_failure( 'speed off tsk'))

        self.speed_pwm_task = loop.create_task(self.speed_pwm_control())
        self.speed_pwm_task.add_done_callback(check_failure('speed pwm tsk'))

        self.speed_step_task = loop.create_task(self.step_speed_control())
        self.speed_step_task.add_done_callback(check_failure('speed steps'))
                    

    #RUN / OPS
    def run(self,vmove=0.001):
        """run program without interactive ensuring that calibration occurs first"""
        loop = asyncio.get_event_loop()
        loop.run_until_complete(self.start_control())
        self.first_feedback = d = asyncio.Future()

        self.set_speed_tasks()

        def go(*args,docal=True,**kw):
            nonlocal self, loop
            self.mark_start()
            log.info(f'feedback OK. cal = {docal}')
            self.set_mode('center')
            
        self.first_feedback.add_done_callback(go)

        try:
            loop.run_forever()

        except KeyboardInterrupt as e:
            log.info("Caught keyboard interrupt. Canceling tasks...")
            self.stop()
            sys.exit(0)
        finally:
            loop.close()



    #STOPPPING / SAFETY
    #TODO: Enable here is for the clearpath motor, A4899 stepper enable is active. low
    #External Control Methods
    async def enable_control(self):
        log.info('enable control')
        if not self.enabled:
            if ON_RASPI:
                val = await self.pi.write(self._motor_en_pin,1)
            self.enabled = True
        else:
            log.info(f'already enabled!')

    async def start_control(self):
        self.mark_start()
        await self.enable_control()
        if self.enabled and self.stopped:
            self.set_speed_tasks()
            self.stopped = False
            await asyncio.sleep(1)
        elif not self.stopped:
            log.info(f'already started!!')
        elif not self.enabled:
            log.info(f'not enabled!')

    async def disable_control(self):
        log.info('disabiling motor!')
        if ON_RASPI:
            await self.pi.write(self._motor_en_pin,0) #disable force
        self.enabled = False

    async def stop_control(self):
        await self.disable_control()
        await self._stop()

    def stop(self):
        loop = asyncio.get_event_loop()
        if loop.is_running:
            loop.call_soon(self._stop)
        else:
            loop.run_until_complete(self._stop())     
            loop.run_until_complete(self._close())
        self.stopped = True

    async def _stop(self):
        if DEBUG: log.info(f'task stop')
        self.stopped = True
        await self.sleep(0.1)

        self.set_mode('stop')

        if hasattr(self,'speed_off_task') and not self.speed_off_task.cancelled:
            self.speed_off_task.cancel()
        
        if hasattr(self,'speed_pwm_task') and not self.speed_pwm_task.cancelled:
            self.speed_pwm_task.cancel()

        if hasattr(self,'speed_step_task') and not self.speed_step_task.cancelled:
            self.speed_step_task.cancel()

        await self.sleep(0.1)
        if ON_RASPI:

            #Set PWM Drive off
            log.info(f'setting pwm off')
            try:
                pt = await self.pi.set_PWM_dutycycle(self._vpwm_pin,0)
                #vpt = await self.pi.write(self._vpwm_pin,0)
                vt = await self.pi.set_PWM_dutycycle(self._tpwm_pin,0)
                #tp = await self.pi.write(self._tpwm_pin,0)
            except Exception as e:
                log.info(f'exception turning off pwm: {e}')      

            log.info(f'setting steps off')
            try:
                sp =await self.pi.write(self._step_pin,0)
                dp = await self.pi.write(self._dir_pin,0)
            except Exception as e:
                log.info(f'exception turning off steps: {e}')             

            

            await self._close(stop=False)

            await self.sleep(0.1)           

    async def _close(self,stop=True):
        try:
            await self.pi.wave_tx_stop()
        except Exception as e:
            log.info(f'pigpio wavestop error: {e}')
        
        try:
            await self.pi.wave_clear()
        except Exception as e:
            log.info(f'pigpio close error: {e}')                

        time.sleep(1)
        if stop: await self.pi.stop()


    # async def exec_cb(self,exc,loop):
    #     log.info(f'got exception: {exc}| {loop}')
    #     await self._stop()
    #     #sys.exit(1) #os.kill(os.getpid(), signal.SIGKILL)


    
    def setup_i2c(self,cv_inx = 0,smb=None,lock=None):
        if smb is None:
            self.smbus = smbus.SMBus(1)
        else:
            self.smbus = smb

        if lock is None:
            self.i2c_lock = threading.Lock()
        else:
            self.i2c_lock = lock

        try:
            cb = config_bit(cv_inx,fvinx = 4)
            db = int(f'{dr}00011',2)
            data = [cb,db]
            #do this before reading different pin, 
            log.info(f'setting adc to: {[bin(d) for d in data]}')
            with self.i2c_lock:
                self.smbus.write_i2c_block_data(0x48, 0x01, data)
            #setup alert pin!
            #self.smbus.write_i2c_block_data(0x48, 0x02, [0x00,0x00])
            #self.smbus.write_i2c_block_data(0x48, 0x03, [0x80,0x00])
            self.adc_ready = True

        #TODO: handle i2c failure and restart or reattempt

        except Exception as e:
            log.error('issue setting up temp',exc_info=e)
            self.adc_ready = False        

    def is_safe(self):
        #base = any((self._control_mode_fail_parms.values()))
        base = False
        if self.drive_mode in self._control_mode_fail_parms:
            base = self._control_mode_fail_parms[self.drive_mode]
        else:
            log.warning(f'no drivemode found: {self.drive_mode}')
        return all([not base,
                    not self.fail_sc,
                    not self.fail_st])
    
    def set_mode(self,new_mode):
        log.info(f'setting mode: {new_mode}')
        new_mode = new_mode.strip().lower()
        assert new_mode in drive_modes,f'bad drive mode {new_mode}! choose: {drive_modes}'
        new_mode = new_mode.lower().strip()

        self.err_int = 0 #reste pid
        self.mark_start()
        self.last_print = 0

        if new_mode == self.drive_mode:
            if DEBUG: log.info(f'same drive mode: {new_mode}')
            if new_mode == 'stop':
                self.v_cmd = 0 #safe repeat
            return
        
        self.drive_mode = new_mode
        log.info(f'set mode: {self.drive_mode}')
        if hasattr(self,'mode_changed'):
            self.mode_changed.set_result(new_mode)
        self.mode_changed = asyncio.Future()
    
    def set_speed_mode(self,new_mode):
        new_mode = new_mode.strip().lower()
        assert new_mode in speed_modes,f'bad speed mode {new_mode}! choose: {speed_modes}'
        new_mode = new_mode.lower().strip()
        if new_mode == self.speed_control_mode:
            log.info(f'same speed mode: {new_mode}')
            return
        
        self.speed_control_mode = new_mode
        log.info(f'setting speed mode: {self.speed_control_mode}')
        if hasattr(self,'speed_control_mode_changed'):
            self.speed_control_mode_changed.set_result(new_mode)
        self.speed_control_mode_changed = asyncio.Future()        

    def make_control_mode(self,mode,loop_function):
        loop = asyncio.get_event_loop()
        #make the loop task
        func = self.control_mode(loop_function,mode)
        
        
        #task.add_done_callback #TODO: handle failures
        self._control_modes[mode]=None #not started
        self._control_mode_fail_parms[mode] = False

        def _fail_control(res):
            log.info(f'mode done! {mode}')
            try:
                res.result()
            
            except MovementError:
                self.v_cmd = 0
                loop.run_until_complete(self.run_stop())
                self.set_speed_mode('stop')

            except Exception as e:
                traceback.print_exception(e)

        task = loop.create_task(func)
        self._control_modes[mode]=task
        task.add_done_callback(_fail_control)
        return task
        



    def setup_control(self):
        log.info('starting...')
        assert self.adc_ready, f'cannot run without feedback!'

        loop = asyncio.get_event_loop()
        self.set_mode('stop')
        self.started = asyncio.Future()
        

        self.goals_task = self.make_control_mode('wave',self.wave_goal)
        self.stop_task = self.make_control_mode('stop',self.run_stop)
        self.center_task = self.make_control_mode('center',self.center_head)



    #CONTROL MODES
    async def control_mode(self,loop_function:callable,mode_name:str):
        """runs an async function that sets v_cmd for the speed control systems"""
        log.info(f'creating control {mode_name}|{loop_function.__name__}...')
        
        while True:
            start_mode = self.mode_changed

            if (isinstance(mode_name,str) and self.drive_mode == mode_name) or (isinstance(mode_name,(list,tuple)) and self.drive_mode in mode_name):
                log.info(f'starting control {mode_name}|{loop_function.__name__}...')
                try: #avoid loop overhead in subloop
                    while self.is_safe() and start_mode is self.mode_changed:
                        await loop_function() #continuously call zit
                        self._control_mode_fail_parms[mode_name] = False
                    if not self.is_safe():
                        log.warning(f'no longer safe, exiting {mode_name} control')
                        await self._stop()
                except Exception as e:
                    self._control_mode_fail_parms[mode_name] = True
                    log.info(f'control {mode_name} failure|{loop_function.__name__} error: {e}')
                    task = asyncio.current_task()
                    traceback.print_tb(e)
            
            #if your not the active loop wait until the mode has changed to check again. Only one mode can run at a time
            await self.mode_changed

        log.warning(f'control io ending...')
        await self._stop()

    #Control
    async def pid_control(self,v_goal,enf_max=None):
        t = time.perf_counter()
        fv = self.feedback_volts
        err = vdir_bias*(v_goal-fv)
        self.z_err = err * self.dzdvref
        #if DEBUG: 
        #TODO: integral windup prevention
        self.err_int = self.err_int + err*self.dt

        Vp = err * self.kp_zerr
        Vi = self.err_int * self.ki_zerr
        Vd = self.dvdt_10 * self.kd_zerr

        if self.last_print > t:
            self.last_print = 0
        if t - self.last_print > print_interavl:
            self.last_print = t
            log.info(f'PID e:{err:5.4f}|ei:{self.err_int:5.4f}|P:{Vp:5.4f}|I:{Vi:5.4f}|D{Vd:5.4f}')        

        if enf_max is not None:
            self.v_cmd = min(max(Vp+Vi+Vd,-self.act_max_speed*enf_max),self.act_max_speed*enf_max)

        await self.sleep(self.control_interval)

        return err

    async def center_head(self,find_tol = 0.01,set_mode=False):
        err = await self.pid_control(self.safe_vref_0,enf_max=0.1)
        self.z_wave = 0
        self.v_wave = 0
        if set_mode is not False and abs(err)<find_tol:
            self.set_mode(set_mode)
            return
        #print(self.zero_frac,self.upper_frac,self.lower_frac)
        
    async def wave_goal(self):
        ###constantly determines
        t = time.perf_counter()
        


        self.z_wave = self.wave.z_pos(t-self.start)
        self.v_wave = vw = self.wave.z_vel(t-self.start)
        if WAVE_VCMD_DIR:
            #position correction over periods
            teval = self.wave.ts #TODO: add frac input
            alpha = self.dt / teval
            self.z_err = err = vdir_bias*(self.z_wave - self.z_cur) #avg should be zero
            self.err_int = self.err_int*(1-alpha) + err * alpha
            
            vcorr = err * self.kp_zerr + self.err_int * self.ki_zerr
            self.v_cmd = self.v_wave + vcorr
            await self.sleep(self.control_interval)

            if self.last_print > t:
                self.last_print = 0
            if t - self.last_print > print_interavl:
                self.last_print = t
                log.info(f'PID e:{err:5.4f}|i:{self.err_int:5.4f}|vc:{vcorr:5.4f}|vw:{vw:5.4f}')

        else:
            v_goal = self.hwave_to_v(self.z_wave)
            err = await self.pid_control(v_goal)
        #print(self.zero_frac,self.upper_frac,self.lower_frac)

    #Wave Control Goal
    async def set_dir(self,dir=None):
        if dir is None:
            dir = self._last_dir
        else:
            self._last_dir = dir
        await self.pi.write(self._dir_pin,1 if dir > 0 else 0)

    async def run_stop(self):
        self.v_cmd = 0
        self.z_wave = 0
        self.v_wave = 0
        await self.sleep(self.control_interval)
                    

    #Saftey & FEEDBACK
    #safe bounds and references
    def update_const(self):
        self.dz_per_step = self.dz_per_rot / self.steps_per_rot
        self.dvref_range = self.upper_v - self.lower_v
        log.info(f'setting dzdv = {self.dz_range} <> [3.3/{self.dvref_range}]')
        self.dzdvref = self.dz_range/(self.v_max - self.v_min)

    def hwave_to_v(self,h_in):
        dvf = (h_in/self.dzdvref) + self.safe_vref_0

        ul = self.v_max - self.v_min
        vu = ul * self.upper_frac
        vl = ul * self.lower_frac
        
        return min(max(dvf,vl),vu)
    

    def v_to_hwave(self,v_in):
        ul = self.v_max - self.v_min
        vu = ul * self.upper_frac
        vl = ul * self.lower_frac
        v_in = min(max(v_in,vl),vu)  

        return (self.feedback_volts - self.safe_vref_0)*self.dzdvref


    @property
    def feedback_pct(self):
        fb = self.feedback_volts
        fb = 0 if fb is None else fb
        return (fb - self.lower_v)/ (self.upper_v - self.lower_v)
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

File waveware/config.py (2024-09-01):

import logging
import diskcache
import logging
import pathlib
import os

import pytz
import datetime
import pigpio
import sys

import traceback
from math import cos,sin
from decimal import Decimal

DEBUG = os.environ.get('WAVEWARE_DEBUG','false').lower().strip()=='true'
base_log = logging.INFO
if DEBUG:
    base_log = logging.DEBUG

BASIC_LOG_FMT = "%(asctime)s|%(message)s"
logging.basicConfig(level=base_log,format=BASIC_LOG_FMT)
log = logging.getLogger("conf")

mm_accuracy_enc = Decimal('1e-3')
mm_accuracy_ech = Decimal('1e-4')

pst = pytz.timezone('US/Pacific')
utc = pytz.utc

def to_test_time(timestamp):
    dt = datetime.datetime.fromtimestamp(timestamp,tz=pytz.UTC)
    return dt.astimezone(pst)

def to_date(timestamp):
    return to_test_time(timestamp).date()

if 'AWS_PROFILE' not in os.environ:
    log.info(f'setting AWS_PROFILE to `wavetank`')
    os.environ['AWS_PROFILE'] = aws_profile = 'wavetank'
else:
    aws_profile = os.environ.get('AWS_PROFILE','wavetank')
    log.info(f'loaded AWS_PROFILE to `{aws_profile}`')

#positive vdir indicates positive velocity increases z.
vdir_bias = -1 

#MOCK Specifications
mock_mass_act = 2.5
mock_act_fric = -0.005


mock_bouy_awl = 0.01 #10cm2
mock_bouy2_awl = 0.0001 #10cm2
mock_bouy_bwl = -0.001
mock_bouy2_bwl = -0.01
mock_bouy_mass = 0.1
mock_bouy2_mass = 0.5

#IMPORT GPIO / CONFIGURE RASPI
try:
    import RPi.GPIO as gpio
    ON_RASPI = True
    pigpio.exceptions = DEBUG #TODO: make false
    from imusensor.MPU9250 import MPU9250
    import smbus
except:
    ON_RASPI = False
    pigpio.exceptions = DEBUG
    smbus = None
    MPU9250 = None

#S3 Happens by deault ON_RASPI=true or if WAVEWARE_FLDR_NAME==test
LOG_TO_S3 = os.environ.get('WAVEWARE_LOG_S3','true').lower().strip()=='true'
bucket = os.environ.get('WAVEWARE_S3_BUCKET',"nept-wavetank-data")
folder = os.environ.get('WAVEWARE_FLDR_NAME',"V1")
PLOT_STREAM = (os.environ.get('PLOT_STREAM','false')=='true')

FW_HOST = os.environ.get('FW_HOST','0.0.0.0' if ON_RASPI else '127.0.0.1')
embedded_srv_port = int(os.environ.get('WAVEWARE_PORT',"8777"))
REMOTE_HOST = os.environ.get('WAVEWARE_HOST',f'http://{FW_HOST}:{embedded_srv_port}')

WAVE_VCMD_DIR = os.environ.get('WAVEWARE_VWAVE_DIRECT','true').lower().strip()=='true'

drive_modes = ['stop','wave','center']
default_mode = 'wave'

speed_modes = ['step','pwm','off','step-pwm']
default_speed_mode = os.environ.get('WAVE_SPEED_DRIVE_MODE','pwm' if ON_RASPI else 'off').strip().lower()
assert default_speed_mode in speed_modes, f'bad speed mode, check WAVE_SPEED_DRIVE_MODE!'

print_interavl = 0.5 if not DEBUG else 0.1
graph_update_interval = float(os.environ.get('WAVEWARE_DASH_GRAPH_UPT','3.3'))
num_update_interval = float(os.environ.get('WAVEWARE_DASH_READ_UPT','1.5'))
#polling & data range
poll_rate = float(os.environ.get('WAVEWARE_POLL_RATE',1.0 / 33))
poll_temp = float(os.environ.get('WAVEWARE_POLL_TEMP',60))
window = float(os.environ.get('WAVEWARE_WINDOW',6))


log.info(f'Running AWS User: {aws_profile}| {REMOTE_HOST} S3: {bucket} fld: {folder}| DEBUG: {DEBUG}| RASPI: {ON_RASPI}')

path = pathlib.Path(__file__)
fdir = path.parent
cache = diskcache.Cache(os.path.join(fdir,'data_cache','dl_cache.db'))

def check_failure(typ):
    def f(res):
        try:
            res.result()
        except Exception as e:
            log.info(f'{typ} failure: {e}')
            traceback.print_tb(e.__traceback__) 
    return f

#PINS
encoder_pins = [(17,18),(27,22),(23,24),(25,5)]
encoder_sens = [{'sens':0.005*4}]*4
echo_pins = [16,26,20,21]

pins_kw = dict(dir_pin=4,step_pin=6,speedpwm_pin=12,adc_alert_pin=7,hlfb_pin=13,motor_en_pin=19,torque_pwm_pin=10,echo_trig_pin=8)

log.info(f'PIN SETTINGS:')
for i,(a,b) in enumerate(encoder_pins):
    log.info(f'ENCDR CH: {i} A: {a} B:{b}')

for i,ep in enumerate(echo_pins):
    log.info(f'ECHO CH: {i} A: {ep} TRIG: {pins_kw["echo_trig_pin"]}')

for k,p in pins_kw.items():
    log.info(f'{k.upper()}: {p}')


#PINS
#parameter groupings
z_wave_parms = ['z_cur','z_err','z_wave','v_cur','v_cmd','v_wave','wave_fb_pct','wave_fb_volt']
z_sensors = [f'z{i+1}' for i in range(4)]
e_sensors = [f'e{i+1}' for i in range(4)]

zgraph = ['z_cur','z_err','z_wave']
vgraph = ['v_cur','v_cmd','v_wave']
acclgryo = ['az','ax','ay','gx','gy','gz','mz']

wave_drive_modes = ['stop','center','wave']
M = len(wave_drive_modes)
mode_dict = {i:v.upper() for i,v in enumerate(wave_drive_modes)}

wave_inputs = ['mode','wave-steep','wave-hs','z-ref','z-range','trq-lim']
Ninputs = len(wave_inputs)

all_sys_vars = z_wave_parms+z_sensors+e_sensors #output only
all_sys_parms = z_wave_parms+z_sensors+e_sensors+wave_inputs
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

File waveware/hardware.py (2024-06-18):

"""Module to control and gather data from raspberry system

#Motion Demand:
#Hs - significant wave height run
#Ts - significant wave period

#Data Input / Record:
#waterlevel - height from bottom
#comment 

#Calibration
#z_ref - test_reference point in absolute space

Control:
#mode 1: stepper position / velocity control
#mode 2: two position toggle
#enable - 0 enabled, 1 - disabled
#Ach - dir
#Bch - step

Data Aquired:
#t - time relative to start time
#Pa - atmospheric pressure (I2C)
#Ta - atmospheric temp (I2C)
#H_xi - wave height measured at distance xi 2-4 (echoPin/GPIO)
#z_pos - current encoder z height minus z_ref (A/B/GPIO)
#z_act - actuator height (ADC)
#ax,ay,az - current accelerations (I2C)
#gx,gy,gz - current gyro (I2C)
#hlfb - PPR / PWM speed (GPIO)

# DATA STORAGE:
Store Data in key:value pandas format in queue format
all items will have a `timestamp` that is use to orchestrate using `after` search, items are moved from the buffer to the cache after they have been processed, with additional calculations.
"""

import asyncio
import threading
import struct

from collections import deque
import signal
import sys

import asyncpio
asyncpio.exceptions = True

import pigpio
import traceback
import datetime
import time
import logging
import json,os
import random

import math

from waveware.control import wave_control
from waveware.data import *
from waveware.config import *


logging.basicConfig(level=logging.INFO)
log = logging.getLogger("hw")



#SI07 temp sensor registers
HUMIDITY = 0xF5
TEMPERATURE = 0xF3
WRITE_HEATER_LEVEL = 0x51
READ_HEATER_LEVEL = 0x11
WRITE_HEATER_ENABLE = 0xE6
READ_HEATER_ENABLE = 0xE7
_RESET = 0xFE


#These exist to test calibration when not running on RPI
FAKE_BIAS = {
                'e1':0.1*(0.5-random.random()) + 0.2*random.random(),
                'e2':0.1*(0.5-random.random()) + 0.2*random.random(),
                'e3':0.1*(0.5-random.random()) + 0.2*random.random(),
                'e4':0.1*(0.5-random.random()) + 0.2*random.random(),
                'z1':1*(0.5-random.random()),
                'z2':1*(0.5-random.random()),
                'z3':1*(0.5-random.random()),
                'z4':1*(0.5-random.random()),
                }

FakeWaveMass = 2
FakeTorque = 5
Ao = 0.0001
Ah = 0.05
Bo = 0
Bh = 0.1
Zh = 0.1

#TODO: model / predict kinematics
def asub(z):
    if z>=0:
        return 0
    fh = min(abs(z)/Zh,1)
    return Ao*(1-fh) + Ah*fh

def bsub(z):
    if z>=0:
        return 0
    fh = min(abs(z)/Zh,1)
    return Bo*(1-fh) + Bh*fh

def fake_wave_stiffness(z):
    if z >= 0:
        return 0
    ah = asub(z)
    return ah * 1000 * 9.81

def fake_wave_damping(z):
    if z >= 0:
        return 0
    ah = asub(z)
    bh = bsub(z)
    return bh * ah * 1000 * 9.81    

class hardware_control:
    
    #hw access
    pi = None

    #pinout / registers
    encoder_conf: list = None #[{sens:x,},...]
    encoder_pins: list = None  #[(A,B),(A2,B2)...]
    echo_pins: list = None #[1,2,3]
    
    #potentiometer_pin: int = None

    #i2c addr
    mpu_addr: hex = 0x68#0x69 #3.3v
    si07_addr: hex = 0x40
    
    #motor control
    control = None

    #config flags
    title: str
    active = False
    poll_rate = poll_rate
    poll_temp = poll_temp
    window = window

    
    #Data Storage
    buffer: asyncio.Queue
    unprocessed: deque
    cache: ExpiringDict
    active_mpu_cal = False

    #TODO: pins_def
    def  __init__(self,encoder_ch:list,echo_ch:list,dir_pin:int,step_pin:int,speedpwm_pin:int,adc_alert_pin:int,hlfb_pin:int,motor_en_pin:int,echo_trig_pin:int,torque_pwm_pin:int,winlen = 1000,enc_conf = None,cntl_conf=None):
        self.start_time = time.perf_counter()
        self.last_time = None

        self.title = f'Test At {datetime.datetime.now().isoformat()}'

        self.default_labels = LABEL_DEFAULT
        self.labels = self.default_labels.copy()
        
        #data storage
        self.buffer = asyncio.Queue(winlen)
        self.unprocessed = deque([], maxlen=winlen)
        
        #TODO: move to global
        self.cache = memcache

        self.i2c_lock = threading.Lock()

        self.last = {} #last set of signals for GPIO
        self.record = {} #for i2c values
        self.echo_pins = echo_ch
        self.encoder_pins = encoder_ch
        if enc_conf is None:
            self.encoder_conf = [{'sens':0.005*4}]*len(self.encoder_pins)
        else:
            assert len(enc_conf) == len(self.encoder_pins), f'encoder conf mismatch'
            self.encoder_conf = enc_conf

        #Echo X pos for wave calc
        self.echo_x1 = 0
        self.echo_x2 = 0
        self.echo_x3 = 0
        self.echo_x4 = 0

        self._motor_en_pin = motor_en_pin
        #stepper
        self._dir_pin = dir_pin
        self._step_pin = step_pin
        #clearpath
        self._speedpwm_pin = speedpwm_pin
        self._torque_pwm_pin = torque_pwm_pin
        self._hlfb_pin = hlfb_pin #io HighLevelFeedback
    
        #adc_alert
        self._adc_alert_pin = adc_alert_pin
        self._echo_trig_pin = echo_trig_pin

        if cntl_conf is None: 
            cntl_conf = {} #empty
        
        self.pi = asyncpio.pi()
        self.control = wave_control(self._dir_pin,self._step_pin,self._speedpwm_pin,self._adc_alert_pin,self._hlfb_pin,self._torque_pwm_pin,motor_en_pin,pi=self.pi,**cntl_conf)

        #Count Up Runs
        self.run_num_id = 0
        self.run_summary = {}

    #Run / Setup
    async def sig_cb(self,*a,**kw):
        log.info(f'got signals, killing| {a} {kw}')
        try:
            await self._stop()
        except Exception as e:
            log.info(f'fail in stop: {e}')
        os.kill(os.getpid(), signal.SIGKILL)
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

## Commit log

2024-04-20 add sonar example
2024-04-21 add encoder
2024-04-21 rmv print
2024-04-21 convert sonar demo to mode 3: analog pulse
2024-04-21 more prints
2024-04-21 update print
2024-04-22 Apply Statsh & Remove Creds
    [b8dfbb69-HEAD.csv]
2024-04-23 split module into components: - add hw, main_fw and data_server from data_acq - moving from global vars to stateful-hwclass - sketched async-drivers (sonar/z-encoder/mpu/temp)
2024-04-25 Add encoder async
2024-04-26 callback encoder
2024-04-26 async print
2024-04-26 better printing
2024-04-26 thread and async
2024-04-26 encoder fix
2024-04-26 Revert "format output"
    This reverts commit fd46c5b6661d0686a1dbe38555d137cfd47d11ff.
    [hardware.py]
2024-04-27 add imu
2024-04-27 imu bug fix
2024-04-27 no i2c
2024-04-27 debug prints
2024-04-27 no read loop in thread
2024-04-27 try print fail
2024-04-27 print floats
2024-04-27 add temp sensor
2024-04-29 add motor control
2024-05-01 no fb pin
2024-05-01 fix filter
2024-05-02 print volts in control
2024-05-04 Speed Drive Mode (pwm,step,off) split between pins Drive Modes spec speed or manually drive modes
2024-05-04 fix prints
2024-05-04 binary print
2024-05-04 null volts
2024-05-04 print on mode change
2024-05-04 print vcmd
2024-05-04 mod wave print
2024-05-04 add calibrate
2024-05-05 print rel
2024-05-05 raise and print
2024-05-05 print lims
2024-05-05 no prints
2024-05-05 print wave errors
2024-05-06 print the thing
2024-05-06 no printy
2024-05-06 wave goal print
2024-05-06 save calibration file
2024-05-09 Merged Control and Sensors: - comples locally starting remote debug git comit stream :) - lowered calibration speeds - added complex mpu-calibrate script to get around libraries input() request by mo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
2024-05-11 exit on main fail
    [control.py, data_server.py, fw_main.py]
2024-05-11 i2c mixed data handiling
2024-05-11 print errrs
2024-05-11 prints alot
2024-05-12 print when active
2024-05-12 print on sleep
2024-05-12 fix plotting and sensor name
    [config.py, data_server.py, hardware.py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]
2024-05-12 print last from pins
2024-05-12 set current
2024-05-12 log not print
2024-05-12 Working IO Buttons
2024-05-15 Added MPU Cal CLI Option, Removed button until active cal needed.
2024-05-16 Update Set Functionality | Use Get / Set functionality. updates can overwrite-user set input| - you could do constant refresh but that requires tracking 'dirty state'... use color of get button??
2024-05-16 print set
2024-05-16 better prints
2024-05-16 parse filters
2024-05-16 test i2c
2024-05-16 req i2c
2024-05-16 fix print
2024-05-16 give me an error or give me a break
    [data_server.py]
2024-05-16 check pin
2024-05-16 modify fw and print status
2024-05-16 print in debug
2024-05-16 print any task failures or eary exists!
    [control.py, data_server.py, fw_main.py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]
2024-05-17 trace errors
2024-05-17 add more print
2024-05-17 fix pid const refs
    [control.py]
2024-05-17 Try start sensors
2024-05-17 start sensors
2024-05-18 print steps
2024-05-18 no print
2024-05-18 Calibrate program
2024-05-18 print less
2024-05-18 prevent stale cal in rate
    [control.py]
2024-05-19 separate pwm / step modes and add combined `step-pwm` mode
2024-05-20 dir print
2024-05-24 Try PID Control
2024-05-24 less print
2024-05-24 no mode no problem
    [control.py, hardware.py]
2024-05-24 print fv
2024-05-25 Update Z Cmd Values And Print Frac Values
2024-05-25 debug print
2024-05-25 better print
2024-05-25 mod vdir wave with correction
    [control.py]
2024-05-25 add print interval
2024-05-25 try print
2024-05-25 fix torques
2024-05-25 torque ctl
2024-06-06 Added Main View Tab For Data Summary: - added test filters on data summary tab - refined variable limits for test purposes - edit-param source of truth for Hs / Ts limits - made window smaller -unifi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
    [app_comps.py, config.py, control.py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]
2024-06-10 Revised Control - improved bias consideration, fixed issue with error - display error raw and absolute position of wave - display mag/accel data + mocked - add steepness based control based on height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
    [app_comps.py, config.py, control.py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]
2024-06-12 Fix Control Time Input / Dir issues
    [control.py]
2024-09-01 Add design files
    [2756-1.stp, 6730.stp, BOM.xlsx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]

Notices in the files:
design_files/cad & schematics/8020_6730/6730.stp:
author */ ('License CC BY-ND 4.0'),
